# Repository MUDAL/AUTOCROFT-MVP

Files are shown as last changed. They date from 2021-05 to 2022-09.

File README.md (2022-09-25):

# AUTOCROFT-MVP

Autocroft is an automatic irrigation system designed and developed by **IoTeam**.

This codebase is an improved Master-Node Architecture based on one master and several base nodes.  
The base nodes collect data and forward them to the master.  
The master processes data from multiple base nodes and sends to the cloud.  

Some **keypad** functionalities:  
- A:  Forward  
- B:  Backward  
- C:  Up/Down  
- D:  Clear memory/Reset system  
- #:  Select 
- *:  Send data from master to the nodes

# Tested versions  
Version 1.0 and Version 1.1 
Each node will be assigned a subchannel of the 433MHz 
communication system. The master will switch from channel to channel in order to send and receive 
data from the nodes.

# How it works  
The master sends data to the nodes in order for them to make irrigation decisions. Irrigation decisions are made  
once every hour (under automatic control). The master and nodes have a runtime of 26 minutes and they sleep for  
34 minutes every hour.  

# Version 1.1  
Has similar features with version 1.0 but with the following changes:  
1. No Bluetooth and WiFi in the master controller.  
2. No EEPROM in the Nodes.  
3. Use of LCD with I2C GPIO expander for the master controller.  

# Link to documentation  
https://www.researchgate.net/publication/359510238_DESIGN_OF_A_LOW_POWER_AUTOMATIC_IRRIGATION_SYSTEM  

# Prototype  
master_controller
node

# 3D models of prototype PCB  
Screenshot (229)
Screenshot (232)

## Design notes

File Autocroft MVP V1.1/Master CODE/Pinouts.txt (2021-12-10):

1.) HC12 (USART1: PA9, PA10)
2.) BME280 (I2C1: PB6, PB7)
3.) EEPROM module (I2C1: PB6, PB7)
4.) RTC module (I2C1: PB6, PB7)
5.) LCD (I2C1: PB6, PB7)
6.) Keypad (PA4-6,PA1,PB1,PB5,PB8,PB9)
7.) WiFi (USART2: PA2,PA3)
8.) Bluetooth (USART3: PB10, PB11)
9.) Wake-up pin (PA0)
10.)HC12 SET pin (PB0)

Pins to reserve:
PA13,PA14,PA15,PB2,PB3,PB4

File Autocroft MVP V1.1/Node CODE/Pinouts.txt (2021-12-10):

1.) HC12 (USART1: PA9, PA10)
2.) Moisture sensor (ADC1: PA5)
3.) Solenoid valve control (GPIO output: PA7)
4.) RTC module (I2C1: PB6, PB7)
5.) RTC INT pin (WKUP: PA0)
6.) HC12 SET pin (PB0)

Pins to reserve:
PA13,PA14,PA15,PB2,PB3,PB4

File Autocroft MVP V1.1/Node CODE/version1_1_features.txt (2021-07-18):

Features to add to next design
1.)MOSFET driver using LM358N Opamp: To power external modules and peripherals down for optimized power consumption.  
2.)Buck converter in place of voltage regulators.

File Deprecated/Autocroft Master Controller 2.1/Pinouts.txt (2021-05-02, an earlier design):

1.) HC06 (USART1: PA9, PA10)
2.) ESP8266 (USART2: PA2, PA3)
3.) GSM module (USART3: PB10, PB11) + 2 additional GPIOs (SMS detect(PA0), reset(PA1))
4.) SD card module (SPI1: PA4, PA5, PA6 and PA7)
5.) 1 or 2Buttons
6.) 3 LEDs

Pins to reserve:
PA13,PA14,PA15,PB2,PB3,PB4

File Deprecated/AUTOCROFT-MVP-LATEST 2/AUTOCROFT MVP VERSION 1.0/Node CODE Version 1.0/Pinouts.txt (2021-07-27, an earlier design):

1.) HC12 (USART1: PA9, PA10)
2.) EEPROM module (I2C1: PB6, PB7)
3.) Moisture sensor (ADC1: PA5)
4.) Solenoid valve control (GPIO output: PA7)
5.) RTC module (I2C1: PB6, PB7)
6.) RTC INT pin (WKUP: PA0)
7.) HC12 SET pin (PB0)

Pins to reserve:
PA13,PA14,PA15,PB2,PB3,PB4

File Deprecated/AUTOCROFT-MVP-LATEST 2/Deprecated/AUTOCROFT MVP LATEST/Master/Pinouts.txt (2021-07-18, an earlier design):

1.) HC12 (USART1: PA9, PA10)
2.) BME280 (I2C1: PB6, PB7)
3.) EEPROM module (I2C1: PB6, PB7)
4.) Battery voltage measurement (ADC2: PB1)
5.) RTC module (I2C1: PB6, PB7)
6.) SD card module (SPI1: PA4, PA5, PA6 and PA7)
7.) LCD (PA11 and PA12 for RS and Enable) (PB12, PB13, PB14 and PB15 for data lines)
8.) State machine Buttons (PB5, PB8, PB9, PB10, PB11)
9.) Button to send master data to node (PA0)
10.) Potentiometer (ADC1: PB0)

Pins to reserve:
PA13,PA14,PA15,PB2,PB3,PB4

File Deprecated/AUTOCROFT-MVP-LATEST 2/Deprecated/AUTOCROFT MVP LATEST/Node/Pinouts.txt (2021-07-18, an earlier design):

1.) HC12 (USART1: PA9, PA10)
2.) EEPROM module (I2C1: PB6, PB7)
3.) Moisture sensor (ADC1: PA5)
4.) Battery voltage measurement (ADC2: PA6)
5.) Solenoid valve control (GPIO output: PA7)
6.) RTC module (I2C1: PB6, PB7)
7.) RTC INT pin (WKUP: PA0)

Pins to reserve:
PA13,PA14,PA15,PB2,PB3,PB4

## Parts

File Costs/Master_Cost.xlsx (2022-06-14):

 | Component | Quantity | Price (₦)
 | LCD | 1 | 700
 | Radio module | 1 | 2500
 | Buck converter | 1 | 850
 | Keypad | 1 | 1500
 | EEPROM | 1 | 120
 | Microcontroller | 1 | 1000
 | Battery | 4 | 1600
 | Battery case | 2 | 1200
 | Enclosure | 1 | 800
 | BME280 sensor | 1 | 1300
 | RTC module | 1 | 900
Total price (₦) |  |  | 12470

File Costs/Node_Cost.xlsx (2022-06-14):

 | Component | Quantity | Price (₦)
 | Radio module | 1 | 2500
 | Li-ion battery | 3 | 1200
 | Battery case | 1 | 800
 | Buck converter | 1 | 850
 | Microcontroller | 1 | 1500
 | Solenoid valve | 1 | 1000
 | MOSFET | 1 | 700
 | Op-amp | 1 | 300
 | Moisture sensor | 1 | 500
 | Enclosure | 1 | 600
 | RTC module | 1 | 900
 | Irrigation hose |  | 1000
Total Price (₦) |  |  | 11850

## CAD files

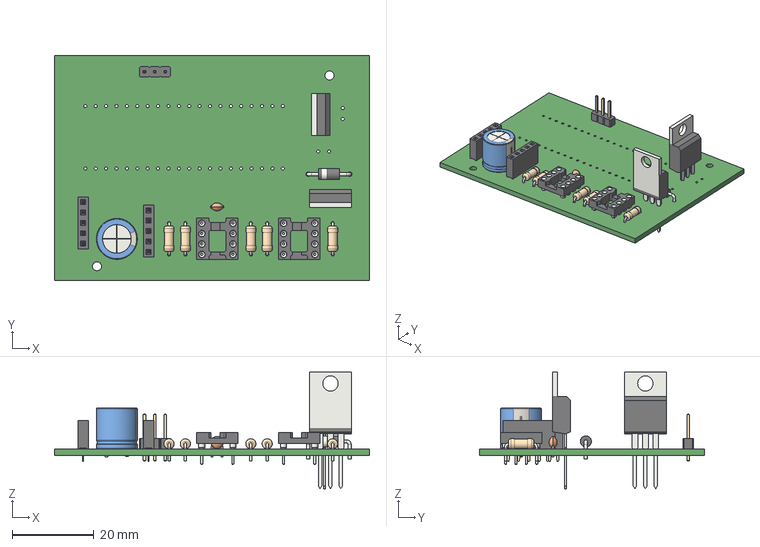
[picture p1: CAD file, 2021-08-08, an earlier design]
AUTOCROFT MVP VERSION 1.0/Node PCB Ver1/Autocroft_node/Autocroft_node.step
77.0 x 55.0 x 28.5 mm

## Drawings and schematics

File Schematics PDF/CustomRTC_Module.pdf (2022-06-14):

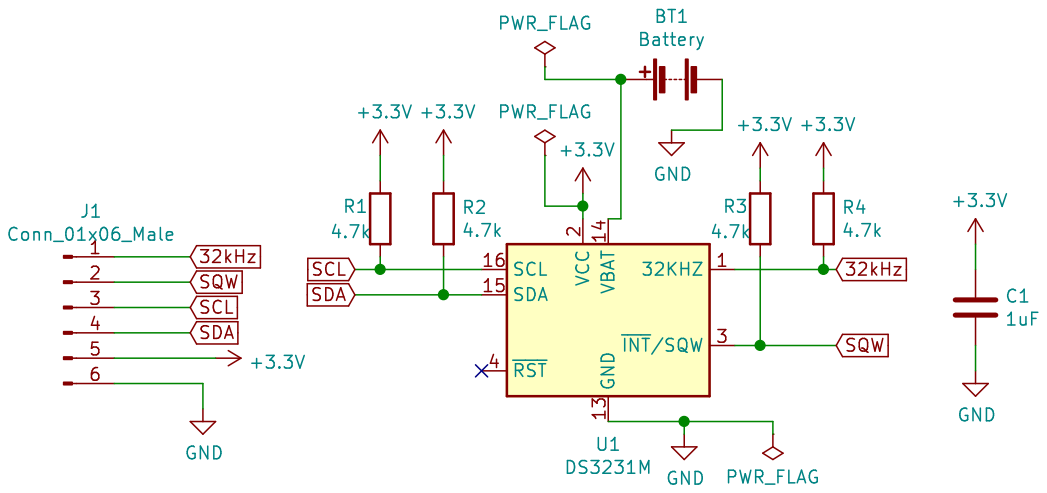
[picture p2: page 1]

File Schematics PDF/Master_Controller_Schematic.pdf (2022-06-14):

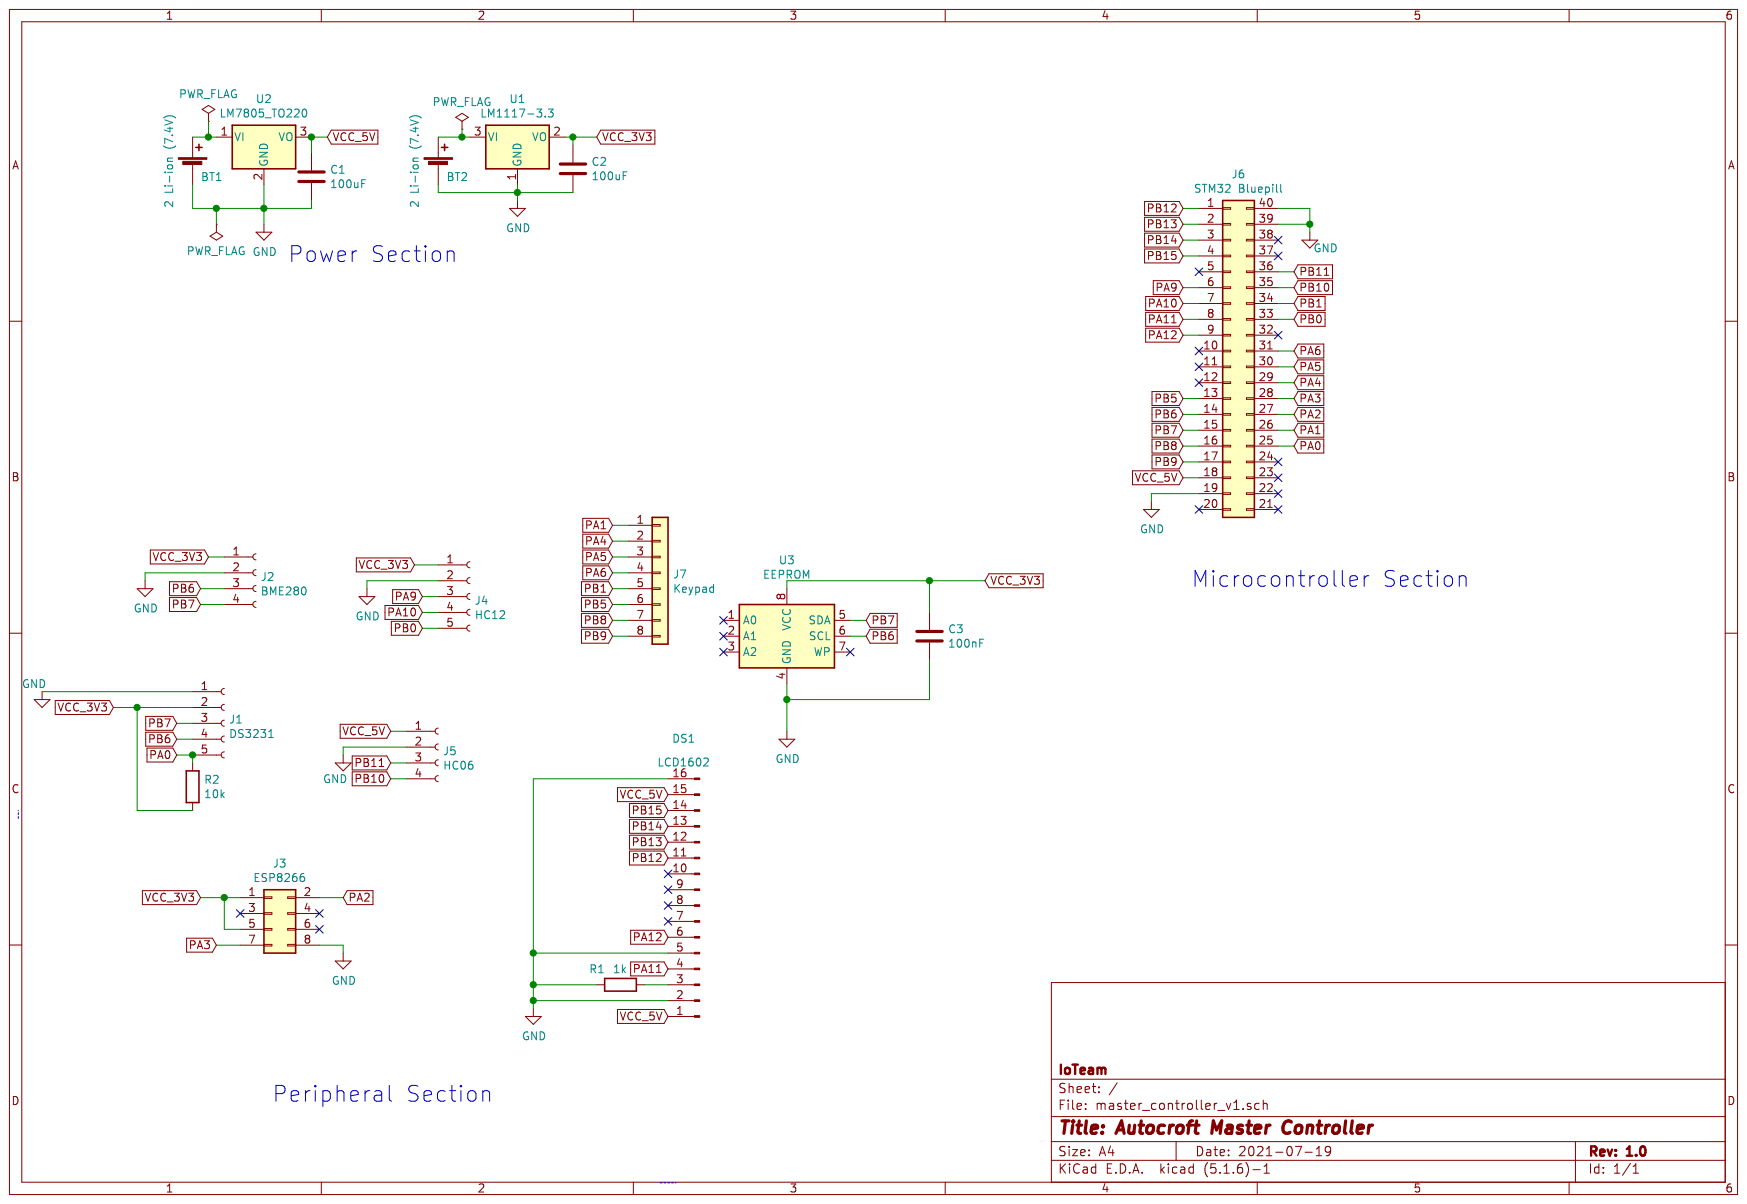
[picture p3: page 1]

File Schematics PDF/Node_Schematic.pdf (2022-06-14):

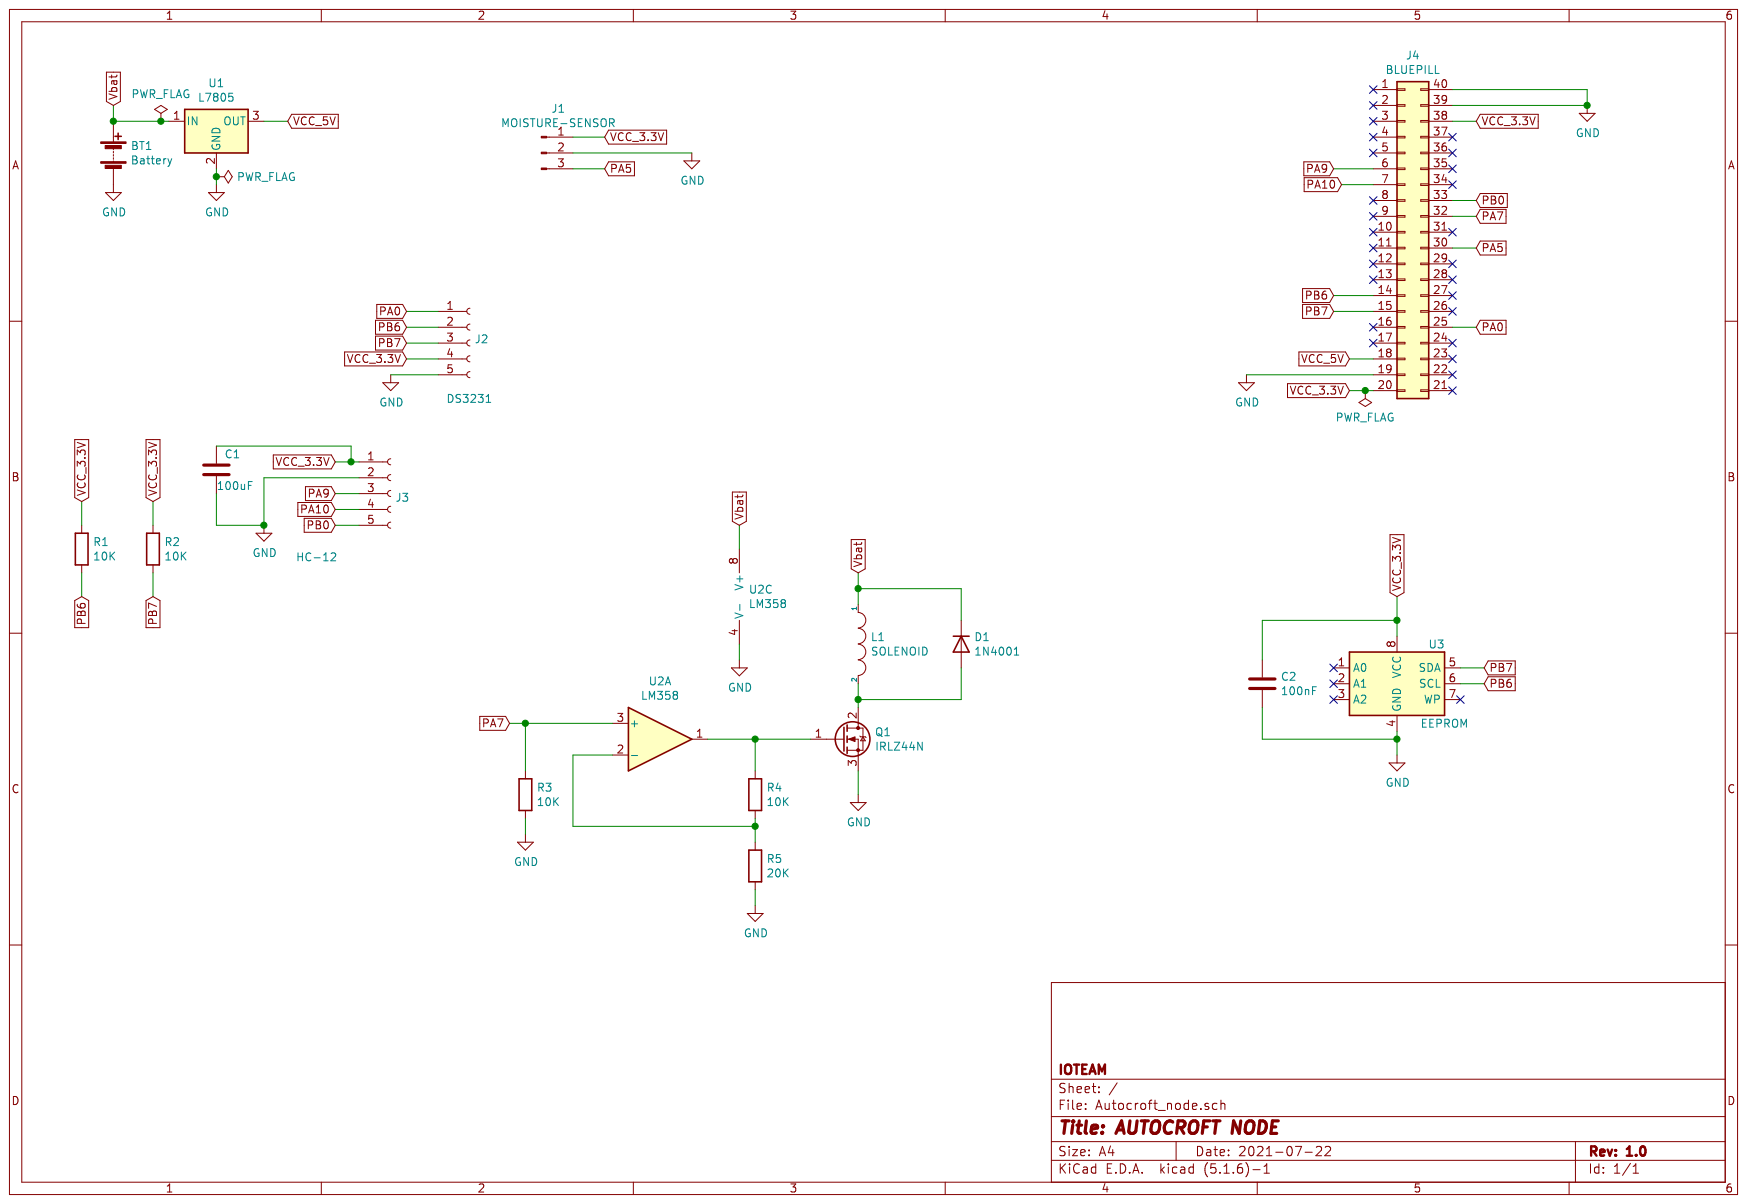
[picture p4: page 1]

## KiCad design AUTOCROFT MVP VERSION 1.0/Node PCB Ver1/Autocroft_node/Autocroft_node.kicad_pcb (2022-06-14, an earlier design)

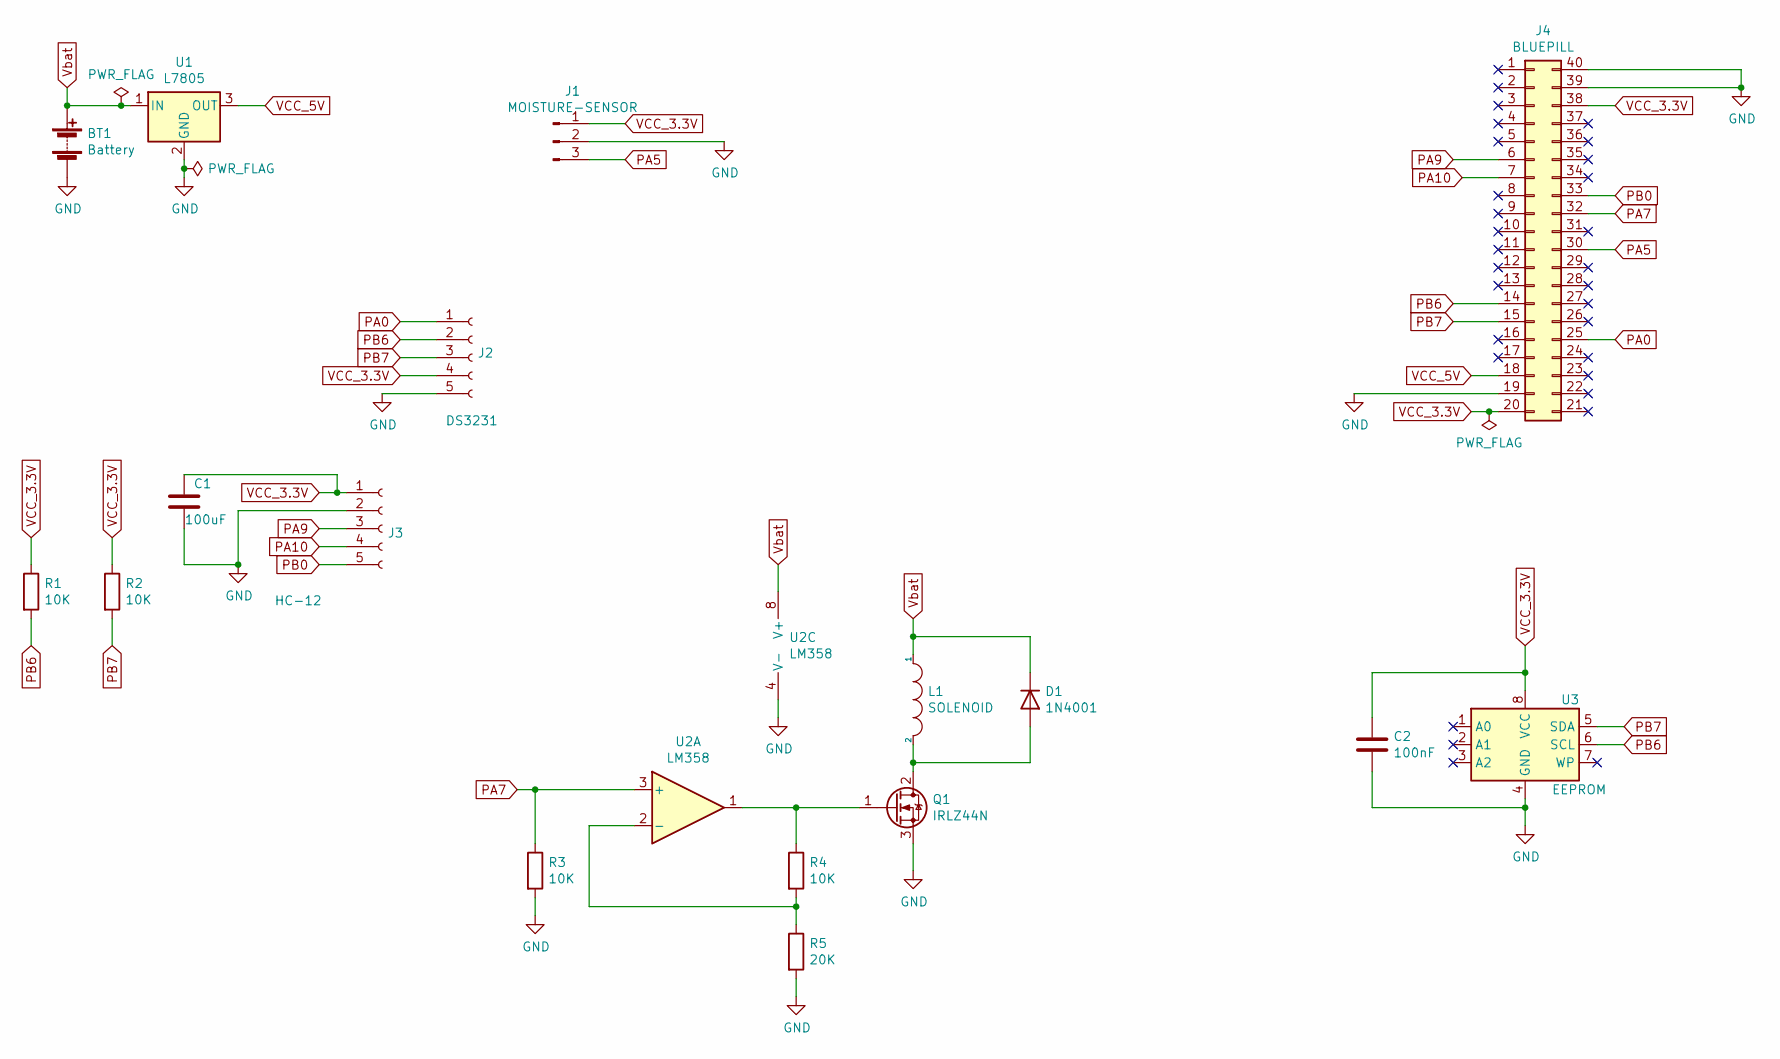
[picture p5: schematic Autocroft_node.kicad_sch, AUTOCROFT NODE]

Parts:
BT1: Battery; BATT
C1: 100uF; CP_Radial_D10.0mm_P5.00mm
C2: 100nF; C_Disc_D3.0mm_W2.0mm_P2.50mm
D1: 1N4001; D_DO-41_SOD81_P10.16mm_Horizontal
J1: MOISTURE-SENSOR; PinHeader_1x03_P2.54mm_Vertical
J2: DS3231; PinSocket_1x05_P2.54mm_Vertical
J3: HC-12; PinSocket_1x05_P2.54mm_Vertical
J4: BLUEPILL
L1: SOLENOID; BATT
Q1: IRLZ44N; TO-220-3_Vertical
R1, R2, R3, R4: 10K; R_Axial_DIN0207_L6.3mm_D2.5mm_P7.62mm_Horizontal
R5: 20K; R_Axial_DIN0207_L6.3mm_D2.5mm_P7.62mm_Horizontal
U1: L7805; TO-220-3_Vertical
U2: LM358; DIP-8_W7.62mm_Socket
U3: EEPROM; DIP-8_W7.62mm_Socket

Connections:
GND: BT1.2 (-), C1.2, C2.2, J1.2, J2.5, J3.2, J4.19, J4.39, J4.40, Q1.3 (S), R3.2, R5.2, U1.2 (GND), U2.4 (V-), U3.4 (GND)
unnamed: D1.2 (A), L1.2, Q1.2 (D)
unnamed: Q1.1 (G), R4.1, U2.1
unnamed: R4.2, R5.1, U2.2 (-)
PA0: J2.1, J4.25
PA5: J1.3, J4.30
PA7: J4.32, R3.1, U2.3 (+)
PA9: J3.3, J4.6
PA10: J3.4, J4.7
PB0: J3.5, J4.33
PB6: J2.2, J4.14, R1.2, U3.6 (SCL)
PB7: J2.3, J4.15, R2.2, U3.5 (SDA)
VCC_3.3V: C1.1, C2.1, J1.1, J2.4, J3.1, J4.20, J4.38, R1.1, R2.1, U3.8 (VCC)
VCC_5V: J4.18, U1.3 (OUT)
Vbat: BT1.1 (+), D1.1 (K), L1.1, U1.1 (IN), U2.8 (V+)

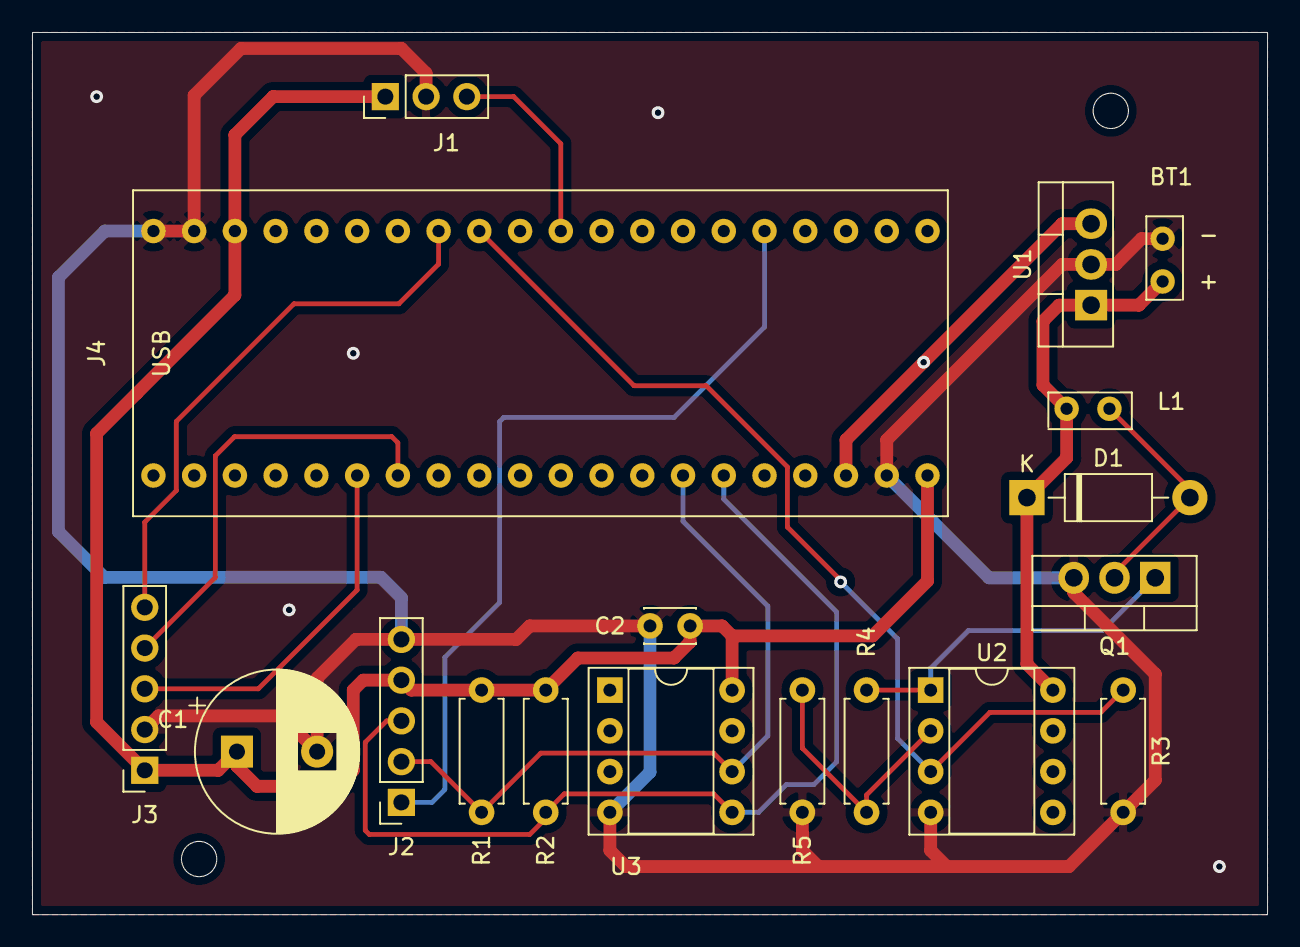
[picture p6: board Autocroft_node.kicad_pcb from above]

Board: 2 copper layers, 77.0 x 55.0 mm, 20 parts (0 on the bottom side), 15 nets.

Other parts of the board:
 : MountingHole_2.2mm_M2
 #2: MountingHole_2.2mm_M2

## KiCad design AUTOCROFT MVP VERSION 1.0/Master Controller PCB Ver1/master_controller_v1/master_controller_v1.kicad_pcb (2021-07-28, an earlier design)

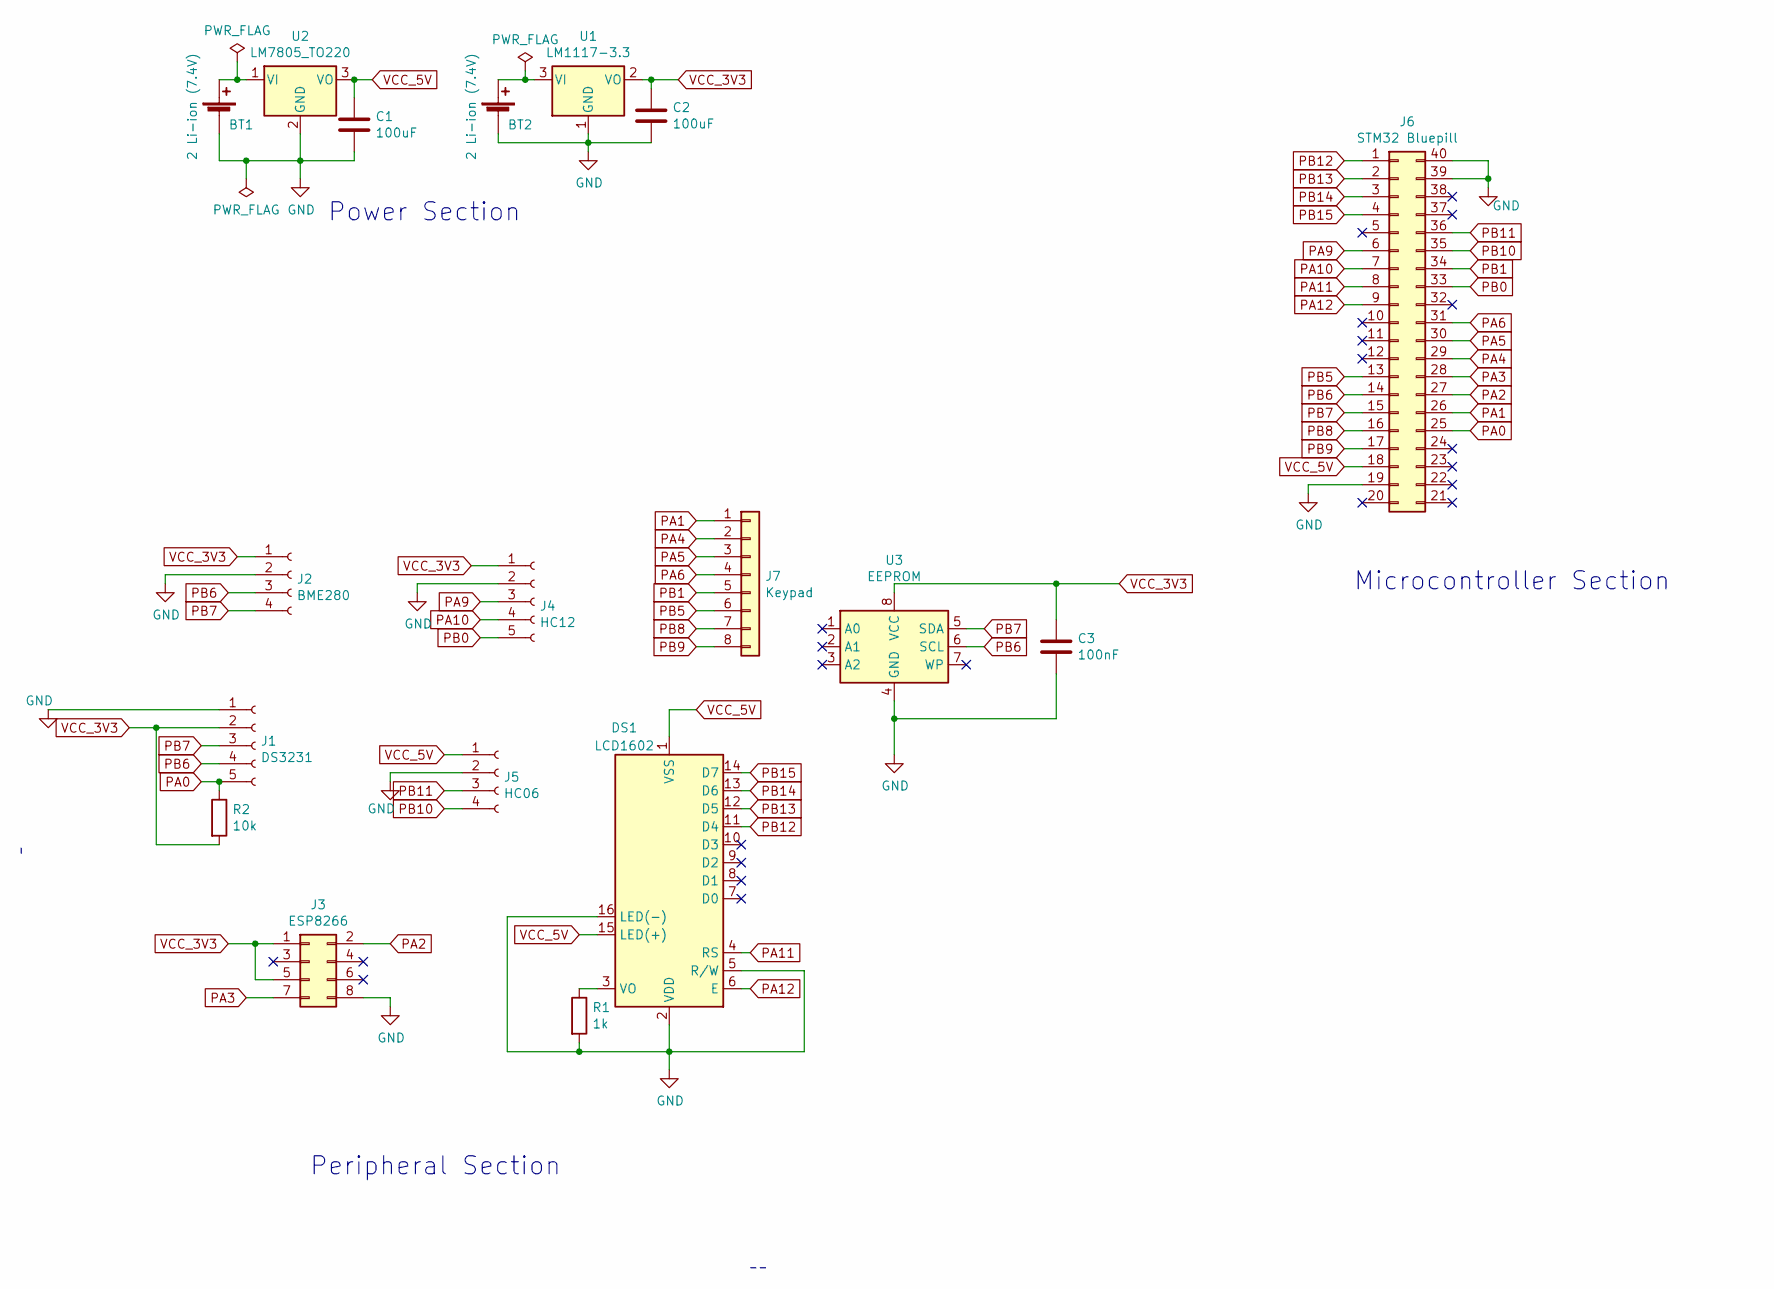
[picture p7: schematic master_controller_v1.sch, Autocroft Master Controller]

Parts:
BT1, BT2: 2 Li-ion (7.4V); BATT
C1, C2: 100uF; CP_Radial_D10.0mm_P5.00mm
C3: 100nF; C_Disc_D3.0mm_W2.0mm_P2.50mm
DS1: LCD1602; PinHeader_1x16_P2.54mm_Vertical
J1: DS3231; PinSocket_1x05_P2.54mm_Vertical
J2: BME280; PinSocket_1x04_P2.54mm_Vertical
J3: ESP8266; PinSocket_2x04_P2.54mm_Vertical
J4: HC12; PinSocket_1x05_P2.54mm_Vertical
J5: HC06; PinSocket_1x04_P2.54mm_Vertical
J6: STM32 Bluepill; BLUEPILL
J7: Keypad; PinHeader_1x08_P2.54mm_Vertical
R1: 1k; R_Axial_DIN0207_L6.3mm_D2.5mm_P7.62mm_Horizontal
R2: 10k; R_Axial_DIN0207_L6.3mm_D2.5mm_P7.62mm_Horizontal
U1: LM1117-3.3; TO-220-3_Vertical
U2: LM7805_TO220; TO-220-3_Vertical
U3: EEPROM; DIP-8_W7.62mm_Socket

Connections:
GND: BT1.2 (-), BT2.2 (-), C1.2, C2.2, C3.2, DS1.2 (VDD), DS1.5 (R/W), DS1.16 (LED(-)), J1.1, J2.2, J3.8, J4.2, J5.2, J6.19, J6.39, J6.40, R1.2, U1.1 (GND), U2.2 (GND), U3.4 (GND)
unnamed: BT1.1 (+), U2.1 (VI)
unnamed: BT2.1 (+), U1.3 (VI)
unnamed: DS1.3 (VO), R1.1
PA0: J1.5, J6.25, R2.1
PA1: J6.26, J7.1
PA2: J3.2, J6.27
PA3: J3.7, J6.28
PA4: J6.29, J7.2
PA5: J6.30, J7.3
PA6: J6.31, J7.4
PA9: J4.3, J6.6
PA10: J4.4, J6.7
PA11: DS1.4 (RS), J6.8
PA12: DS1.6 (E), J6.9
PB0: J4.5, J6.33
PB1: J6.34, J7.5
PB5: J6.13, J7.6
PB6: J1.4, J2.3, J6.14, U3.6 (SCL)
PB7: J1.3, J2.4, J6.15, U3.5 (SDA)
PB8: J6.16, J7.7
PB9: J6.17, J7.8
PB10: J5.4, J6.35
PB11: J5.3, J6.36
PB12: DS1.11 (D4), J6.1
PB13: DS1.12 (D5), J6.2
PB14: DS1.13 (D6), J6.3
PB15: DS1.14 (D7), J6.4
VCC_3V3: C2.1, C3.1, J1.2, J2.1, J3.1, J3.5, J4.1, R2.2, U1.2 (VO), U3.8 (VCC)
VCC_5V: C1.1, DS1.1 (VSS), DS1.15 (LED(+)), J5.1, J6.18, U2.3 (VO)

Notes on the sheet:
Power Section
Peripheral Section
Microcontroller Section

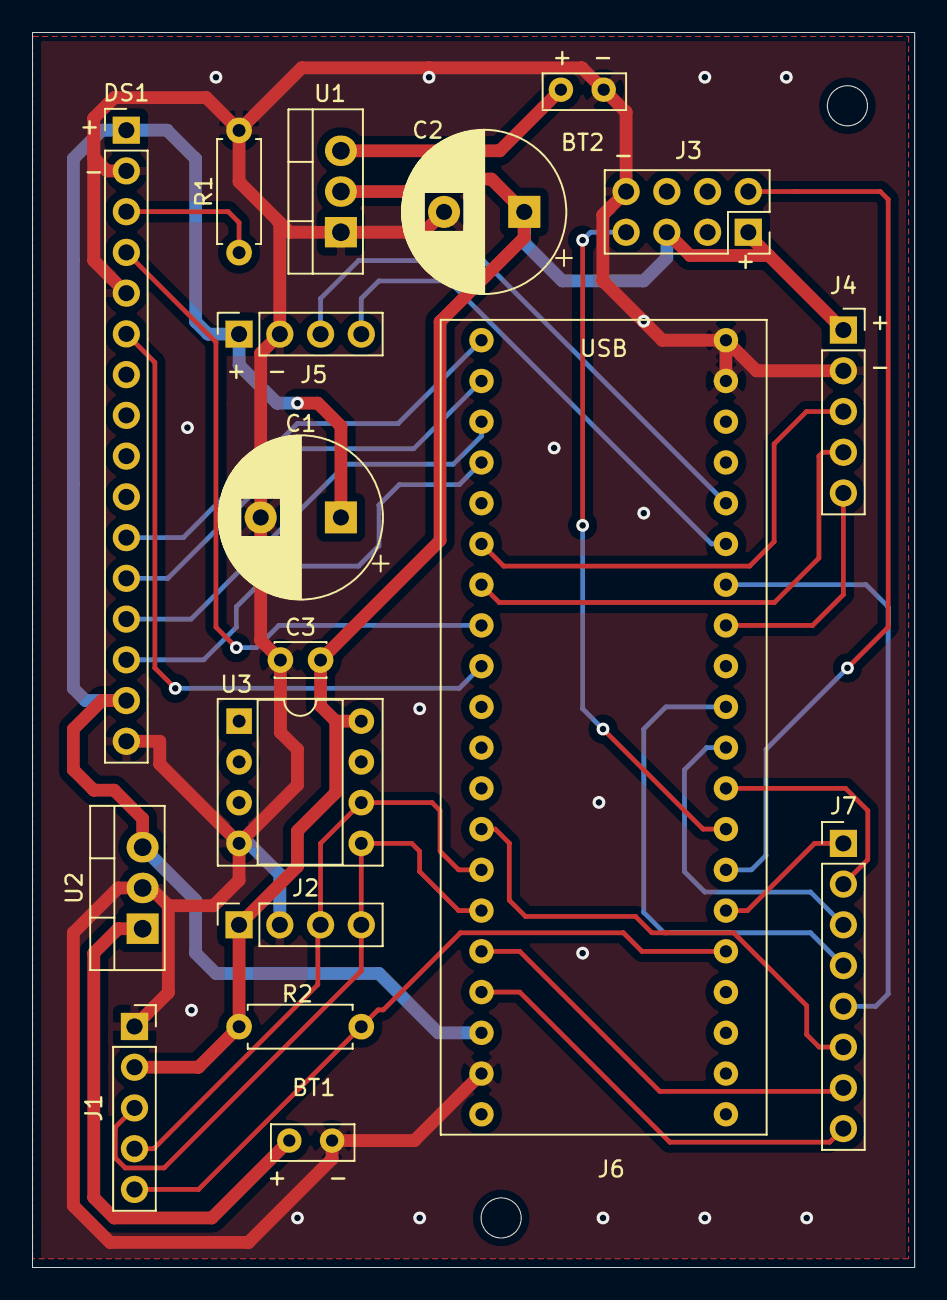
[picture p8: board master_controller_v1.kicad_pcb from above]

Board: 2 copper layers, 55.0 x 77.0 mm, 20 parts (0 on the bottom side), 30 nets.

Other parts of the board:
 : MountingHole_2.5mm
 #2: MountingHole_2.5mm

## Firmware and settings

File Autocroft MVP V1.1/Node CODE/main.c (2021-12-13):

#include <stdint.h>
#include <stdbool.h>
#include "conversions.h"
#include "system.h"
#include "sensor.h"
#include "irrigation.h"
#include "cms.h"
#include "solenoid.h"
#include "ds3231.h"
#include "hc12.h"
#include "communication.h"

/**
@brief Source code for Autocroft Node 
* ID = 0
* Channel number = 1
*/

/**
EEPROM MEMORY ALLOCATION
* PAGE 1: Configuration data from master controller
*/

static void ClearBuffer(uint8_t* pBuffer, uint8_t len)
{
	for(uint8_t i = 0; i < len; i++)
	{
		pBuffer[i] = 0;
	}
}

int main(void)
{
	static NodeRxDataStructure nodeRx;
	static sysTimer_t irrigTimer;
	static ds3231_t rtc;
	static uint8_t soilMoisture;
	//Node parameters
	const uint8_t nodeATcmdLength = 9;
	const uint8_t nodeID = 0;
	uint8_t nodeATcommand[nodeATcmdLength] = "AT+C001\r\n";
	//Sensor variables
	sensorLevel_t moistureLevel = LEVEL_UNDEFINED;
	sensorLevel_t humidityLevel = LEVEL_UNDEFINED;
	sensorLevel_t temperatureLevel = LEVEL_UNDEFINED;
	irrigMethod_t irrigationMethod = IRRIG_METHOD_UNDEFINED;

	//Initializations
	System_Init();
	CMS_Init();
	Solenoid_Init();
	
	HC12_Init();	 
	HC12_RxBufferInit(nodeRx.data, NODE_RX_DATA_SIZE);
	//Channel setting (AT command)
	HC12_SetPinControl(false);
	System_TimerDelayMs(40);
	HC12_TransmitBytes(nodeATcommand, nodeATcmdLength);
	HC12_SetPinControl(true);
	System_TimerDelayMs(80);
	//==================================
	ClearBuffer(nodeRx.data,NODE_RX_DATA_SIZE); //Remove AT command responses
	HC12_RxBufferInit(nodeRx.data, NODE_RX_DATA_SIZE); //Reinitialize node's Rx buffer
	
	DS3231_ResetAlarm2();
	DS3231_24HourFormat();
	DS3231_SetTime(0,0); 
	DS3231_SetAlarm2(0);
	
	while(1)
	{
		/*
		-RECEPTION AND STORAGE OF CONFIGURATION DATA FROM MASTER
		-TRANSMISSION OF MOISTURE DATA TO MASTER
		*/
		if(HC12_RxBufferFull())
		{	
			Node_StoreRxData(&nodeRx);
			
			if(nodeRx.nodeID == nodeID)
			{
				soilMoisture = CMS_GetMoisture();
				HC12_TransmitByte(soilMoisture);
			}	
			if(nodeRx.sysReset)
			{
				DS3231_SetTime(0,nodeRx.rtcMinute);	
				System_Reset();
			}
			moistureLevel = Sensor_GetLevel(soilMoisture, nodeRx.minMoist, nodeRx.maxMoist);			
			humidityLevel = Sensor_GetLevel(nodeRx.humidity, nodeRx.minHum, nodeRx.maxHum);
			temperatureLevel = Sensor_GetLevel(nodeRx.temperature, nodeRx.minTemp, nodeRx.maxTemp);
			irrigationMethod = Irrigation_GetMethod(moistureLevel, humidityLevel, temperatureLevel);
			
			switch(irrigationMethod)
			{
				case NO_IRRIGATION:
				case IRRIG_METHOD_UNDEFINED:
					Solenoid_Control(SOLENOID_OFF);
					break;
				case LIGHT_IRRIGATION:
					//convert minimum irrigation time(minutes) to milliseconds
					System_TimerInit(&irrigTimer,(nodeRx.minIrrigTime*60*1000));
					Solenoid_Control(SOLENOID_ON);
					break;
				case HEAVY_IRRIGATION:
					//convert maximum irrigation time(minutes) to milliseconds
					System_TimerInit(&irrigTimer,(nodeRx.maxIrrigTime*60*1000));
					Solenoid_Control(SOLENOID_ON);
					break;
			}
		}
				
		if(HC12_IncompleteRxData() || (nodeRx.data[0] == IDLE_CHARACTER))
		{
			HC12_RxBufferInit(nodeRx.data, NODE_RX_DATA_SIZE);
		}			
		
		if(Solenoid_IsOn())
		{
			if(System_TimerDoneCounting(&irrigTimer))
			{
				Solenoid_Control(SOLENOID_OFF);
			}
		}

		DS3231_GetTime(&rtc);
		if(rtc.minutes >= SYSTEM_RUNTIME_MINUTES)
		{
			System_GoToStopMode();
			System_Reset();
		}		
	}
}

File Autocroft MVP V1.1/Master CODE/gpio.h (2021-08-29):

#ifndef _GPIO_H
#define _GPIO_H

enum PortRegLevel
{
	GPIO_PORT_REG_LOW = 0,
	GPIO_PORT_REG_HIGH = 1
};

#define GPIO_PULLUP_ENABLE										true
#define GPIO_GEN_PUR_OUTPUT_PUSH_PULL					0x00

#define GPIO_PIN0															0
#define GPIO_PIN0_INPUT_FLOATING							GPIO_CRL_CNF0_0
#define GPIO_PIN0_INPUT_PULLUP_OR_PULLDOWN		GPIO_CRL_CNF0_1
#define GPIO_PIN0_OUTPUT_MODE_2MHZ						GPIO_CRL_MODE0_1
#define GPIO_PIN0_GEN_PUR_OPEN_DRAIN					GPIO_CRL_CNF0_0

#define GPIO_PIN1															1
#define GPIO_PIN1_OUTPUT_MODE_2MHZ						GPIO_CRL_MODE1_1
#define GPIO_PIN1_INPUT_PULLUP_OR_PULLDOWN		GPIO_CRL_CNF1_1

#define GPIO_PIN2_OUTPUT_MODE_2MHZ						GPIO_CRL_MODE2_1
#define GPIO_PIN2_ALT_FUNC_PUSH_PULL					GPIO_CRL_CNF2_1

#define GPIO_PIN3															3
#define GPIO_PIN3_INPUT_PULLUP_OR_PULLDOWN		GPIO_CRL_CNF3_1

#define GPIO_PIN4															4
#define GPIO_PIN4_OUTPUT_MODE_2MHZ						GPIO_CRL_MODE4_1
#define GPIO_PIN4_INPUT_PULLUP_OR_PULLDOWN		GPIO_CRL_CNF4_1


#define GPIO_PIN5					  									5
#define GPIO_PIN5_OUTPUT_MODE_2MHZ						GPIO_CRL_MODE5_1
#define GPIO_PIN5_INPUT_PULLUP_OR_PULLDOWN		GPIO_CRL_CNF5_1
#define GPIO_PIN5_ALT_FUNC_PUSH_PULL					GPIO_CRL_CNF5_1

#define GPIO_PIN6					  									6
#define GPIO_PIN6_OUTPUT_MODE_2MHZ						GPIO_CRL_MODE6_1
#define GPIO_PIN6_INPUT_PULLUP_OR_PULLDOWN 	  GPIO_CRL_CNF6_1
#define GPIO_PIN6_ALT_FUNC_OPEN_DRAIN					GPIO_CRL_CNF6

#define GPIO_PIN7					  									7
#define GPIO_PIN7_ALT_FUNC_OPEN_DRAIN					GPIO_CRL_CNF7
#define GPIO_PIN7_OUTPUT_MODE_2MHZ						GPIO_CRL_MODE7_1
#define GPIO_PIN7_ALT_FUNC_PUSH_PULL					GPIO_CRL_CNF7_1

#define GPIO_PIN8															8
#define GPIO_PIN8_INPUT_PULLUP_OR_PULLDOWN		GPIO_CRH_CNF8_1
#define GPIO_PIN8_OUTPUT_MODE_2MHZ						GPIO_CRH_MODE8_1

#define GPIO_PIN9															9
#define GPIO_PIN9_OUTPUT_MODE_2MHZ						GPIO_CRH_MODE9_1
#define GPIO_PIN9_INPUT_PULLUP_OR_PULLDOWN		GPIO_CRH_CNF9_1
#define GPIO_PIN9_ALT_FUNC_PUSH_PULL					GPIO_CRH_CNF9_1

#define GPIO_PIN10														10
#define GPIO_PIN10_INPUT_PULLUP_OR_PULLDOWN 	GPIO_CRH_CNF10_1
#define GPIO_PIN10_OUTPUT_MODE_2MHZ						GPIO_CRH_MODE10_1
#define GPIO_PIN10_ALT_FUNC_PUSH_PULL					GPIO_CRH_CNF10_1

#define GPIO_PIN11														11
#define GPIO_PIN11_INPUT_PULLUP_OR_PULLDOWN 	GPIO_CRH_CNF11_1
#define GPIO_PIN11_OUTPUT_MODE_2MHZ						GPIO_CRH_MODE11_1

#define GPIO_PIN12														12
#define GPIO_PIN12_OUTPUT_MODE_2MHZ						GPIO_CRH_MODE12_1

#define GPIO_PIN13														13
#define GPIO_PIN13_OUTPUT_MODE_2MHZ						GPIO_CRH_MODE13_1

#define GPIO_PIN14														14
#define GPIO_PIN14_INPUT_PULLUP_OR_PULLDOWN 	GPIO_CRH_CNF14_1
#define GPIO_PIN14_OUTPUT_MODE_2MHZ						GPIO_CRH_MODE14_1

#define GPIO_PIN15														15
#define GPIO_PIN15_INPUT_PULLUP_OR_PULLDOWN 	GPIO_CRH_CNF15_1
#define GPIO_PIN15_OUTPUT_MODE_2MHZ						GPIO_CRH_MODE15_1

//Resets GPIO registers
extern void GPIO_Reset(void);

//Initializes the GPIO to the input mode of choice 
extern void GPIO_InputInit(GPIO_TypeDef* gpioPort, 
													 uint8_t portLevel,  
													 uint8_t gpioPin,
													 uint32_t config,  
													 bool pullupEn);

//Initializes GPIO pins to the input mode of choice
extern void GPIO_MultipleInputInit(GPIO_TypeDef* gpioPort, 
																	 uint8_t portLevel,  
																	 uint16_t gpioPins,
																	 uint32_t config,  
																	 bool pullupEn);

//Initializes the GPIO to the output mode of choice
extern void GPIO_OutputInit(GPIO_TypeDef* gpioPort,
														uint8_t portLevel,
														uint32_t mode,
														uint32_t config);

//Writes a logic 'high' or 'low' to a GPIO pin
extern void GPIO_OutputWrite(GPIO_TypeDef* gpioPort,
														 uint8_t gpioPin,
														 bool gpioPinLogic);

extern void GPIO_OutputClearMultiple(GPIO_TypeDef* gpioPort,uint32_t gpioPins);
extern void GPIO_OutputWriteMultiple(GPIO_TypeDef* gpioPort,uint32_t gpioPins);

//Returns the logic level ( high(true) or low(false) ) of a GPIO input pin
extern bool GPIO_InputRead(GPIO_TypeDef* gpioPort, uint8_t gpioPin);

extern bool GPIO_OutputRead(GPIO_TypeDef* gpioPort, uint8_t gpioPin);

#endif //_GPIO_H

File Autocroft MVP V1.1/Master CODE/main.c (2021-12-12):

#include <stdint.h>
#include <stdbool.h>
#include "conversions.h"
#include "system.h"
#include "bme280.h"
#include "eeprom24c16.h"
#include "hc12.h"
#include "keypad.h"
#include "lcd.h"
#include "ds3231.h"
#include "communication.h"
#include "hmi.h"

/**
@brief Source code for Autocroft Master  
*/

/**
EEPROM MEMORY ALLOCATION
* PAGE 128: Master-to-node data
*/

int main(void)
{
	static uint8_t nodeToMasterData;
	static uint8_t masterToNodeData[MASTER_TX_DATA_SIZE];
	static uint8_t nodeToMasterDataArray[NO_OF_NODES];
	static ds3231_t rtc;

	//Initializations
	System_Init();
	EEPROM_GetData(masterToNodeData,MASTER_TX_DATA_SIZE,PAGE128);
	Keypad_Init();
	LCD_Init();
	HC12_Init();
	HC12_RxBufferInit(&nodeToMasterData,MASTER_RX_DATA_SIZE);
	
	DS3231_ResetAlarm2();
	DS3231_24HourFormat(); 
	DS3231_SetTime(0,0); 
	DS3231_SetAlarm2(0);  
	
	BME280_Init();
	HMI_Init(masterToNodeData,&nodeToMasterData,nodeToMasterDataArray);
	LCD_PrintString("AUTOCROFT");
	LCD_SetCursor(1,0);
	LCD_PrintString("FW: VER 1.1");
	System_TimerDelayMs(800);
	LCD_Clear();
	LCD_PrintString("Initializing....");
	LCD_SetCursor(1,0);
	LCD_PrintString("Please wait");
	
	Master_TransmitReceive(masterToNodeData,
											   MASTER_TX_DATA_SIZE,
												 &nodeToMasterData,
											   nodeToMasterDataArray,
											   NO_OF_NODES);
	while(1)
	{
		HMI_Execute();
		DS3231_GetTime(&rtc);
		if(rtc.minutes >= SYSTEM_RUNTIME_MINUTES)
		{
			EEPROM_StoreData(masterToNodeData,MASTER_TX_DATA_SIZE,PAGE128); 
			LCD_Clear();
			LCD_PrintString("Status: Sleep");
			System_TimerDelayMs(2000);
			LCD_BackLightOff();
			System_GoToStopMode(); 
			System_Reset();
		}
	}
}

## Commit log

2021-04-11 DS3231 PCB design
    The DS3231 module is used for real-time synchronization of nodes in an Autocroft network
2021-04-11 DS3231 PCB design.
    DS3231 RTC module is used for real-time synchronization of nodes in an Autocroft network.
2021-07-19 Master Controller PCB V1
    [master_controller_v1.kicad_pcb, master_controller_v1.sch]
2021-07-20 Progress in design
    [master_controller_v1.kicad_pcb]
2021-07-21 Complete design
    [master_controller_v1-B_Cu.gbl, master_controller_v1-B_Mask.gbs, master_controller_v1-B_Paste.gbp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]
2021-07-21 Improved Silkscreen Placement
    [master_controller_v1-B_Cu.gbl, master_controller_v1-B_Mask.gbs, master_controller_v1-B_Paste.gbp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]
2021-07-26 HC12 SET Pin
    For channel selection
2021-07-27 Autocroft Node
    [Autocroft_node.kicad_pcb, Autocroft_node.sch]
2021-07-27 HC12 Redesign
    Accomodation of 'SET' pin for future software versions and testing.
    [master_controller_v1-B_Cu.gbl, master_controller_v1-B_Mask.gbs, master_controller_v1-B_Paste.gbp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]
2021-07-28 Node PCB
    [Autocroft_node-B_Cu.gbl, Autocroft_node-B_Mask.gbs, Autocroft_node-B_Paste.gbp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]
2021-07-28 folder renamed
    [Autocroft_node-B_Cu.gbl, Autocroft_node-B_Mask.gbs, Autocroft_node-B_Paste.gbp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]
2021-08-08 added STEP files
    [Autocroft_node.step]
2021-08-08 adc changes
2021-08-12 Bill of Materials
    [BOM version 1.0.csv]
2021-08-13 ADC tStab delay
2021-08-22 updated schematic
    [master_controller_v1.sch]
2021-08-22 important updates
    successfully tested
    [Autocroft_node-B_Cu.gbl, Autocroft_node-B_Mask.gbs, Autocroft_node-B_Paste.gbp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]
